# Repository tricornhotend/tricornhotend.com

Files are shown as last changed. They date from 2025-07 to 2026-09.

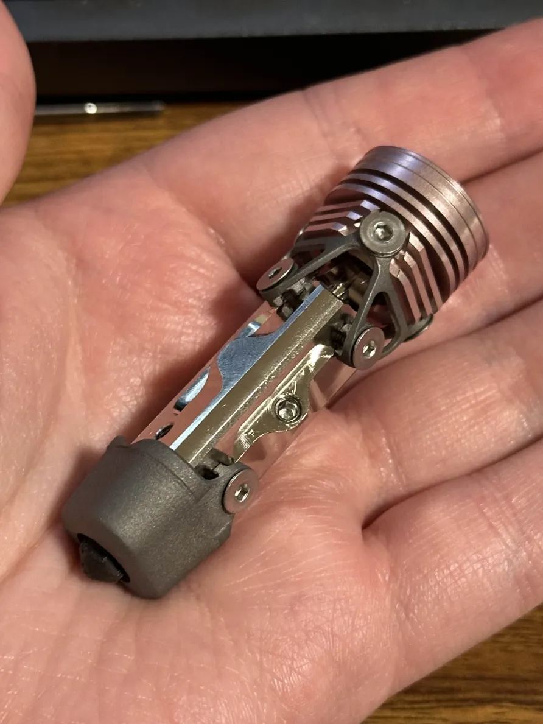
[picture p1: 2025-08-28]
Images/held-tricorn.png

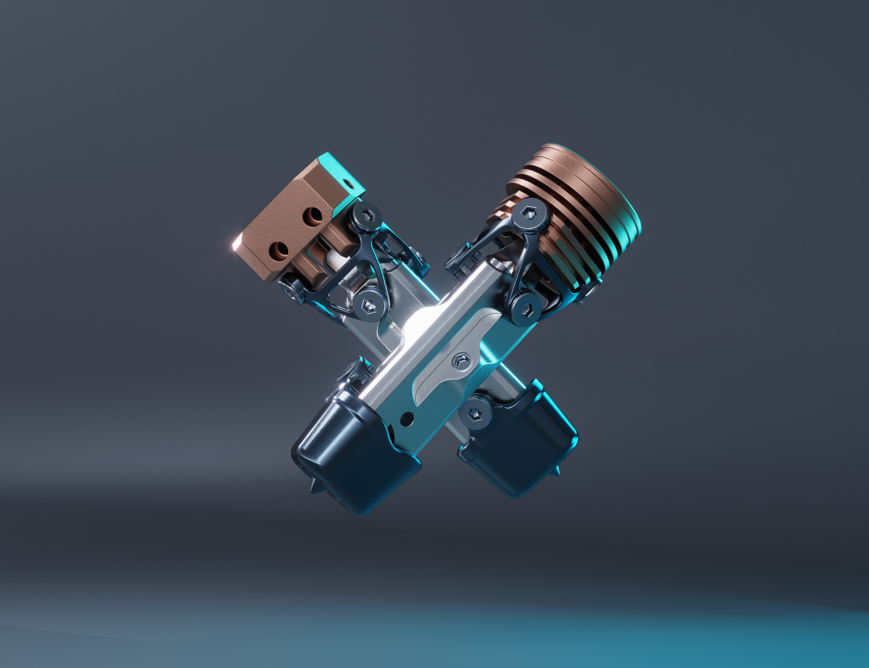
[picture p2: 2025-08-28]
Images/tricornrender.png

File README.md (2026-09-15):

pictures of the hotend cad

Tricorn is a modern open-source hotend featuring mostly standard components while introducing some new ones.
- Inverted heatbreak Tricorn keeps the heatbreak threads out of the meltzone generally improving thermals.
- 4mm Heater cartridges, more combined surface area than 6mm, replacable.
- No screw smaller than m3, everything is either m4 or m3.
- M3 Dragon mounting
- V6 Nozzle Standard
- Air (Fan) or Conduction (Metal plate mounted)
   - (Long) With Hotblock at 260c the Heatsink is passively 118c when unmounted/uncooled in roomtemp env.
- A Long meltzone for it's size.
  - (Long) ~53.5mm with a nozzle, 48mm without.
  - (Short) ~41mm with a nozzle, 35.5mm without.
[Tricorn Website](https://tricornhotend.com)

This project is available under [CC0 1.0 Universal](https://creativecommons.org/publicdomain/zero/1.0/).  
Previous versions were licensed under [CC BY-NC 4.0](https://creativecommons.org/licenses/by-nc/4.0/) and may continue to be used under those terms.  

# Awesome vendors
These are vendors I personally trust to provide a quality version of the hotend, while it can be purchased elsewhere I recommend you purchase from them!

| Vendor | Link | Long | Short |
|---|---|---|---|
| Excit3D | [excit3dprints.com](https://excit3d.shop/shop/tricorn-hotend) | ✅ | ⏲️ |

# Toolhead Support
- [Takeoff toolhead](https://github.com/Kizime123/Takeoff-Toolhead/tree/main) Requires drilling out holes to m3 with a drilling jig.
- [Dual 3628 K3 toolhead](https://github.com/stackingdeezlayers/Annex-K3-SLM-Toolhead)
- ["Trinicorn"](https://github.com/Martin-Ivanc/Trinicorn-Toolhead)

# Hot-end Parts BOM

# Proprietary
- Hot-block
- Heat-sink
- 3x Heaters (D4x40mm, 24v, 40w per, 120w total)
- PT1000 M3x3mm Thermistor
- SLM Shield
- SLM Brace
- Heat-break

# Off The Shelf
- https://www.mcmaster.com/93395A198 (7x structural/shield screws per hot-end)
- https://www.mcmaster.com/92605A522 (3x grub screws per hot-end)
- https://www.mcmaster.com/90666A104 (Optional mounting screws, 4x per hot-end)
- https://www.mcmaster.com/7289A12 (Optional hex key for all screws & heatbreak, 1x)

# General Material recommendations:
- Heatbreak - Ti-6Al-4v (Titanium)
- SLM Shield/Crown - Ti-6Al-4v (Titanium)
- Heatsinks - 6061 Aluminum + (Anodize rose gold)
- Hotblock - UNS C18150 (Copper) + (Electroless Nickel)
- Fasteners - 316 Stainless Steel

# Credit
[Synoon](https://synoon.portfoliobox.net/) - Banner render

# Some other neat hotends
Maybe Tricorn doesn't fit what you are looking for, maybe check out these!  
  
[Chube](https://chubehotend.com/) - Practically indestructible  
[V9](https://www.v9hotend.com/) - Inverted heatbreak & Steel

# Donate
Like the hotend? Doing something cool with the concept? Want to support me?
Protect 🏳️‍⚧️ rights: [https://action.aclu.org/give/now](https://action.aclu.org/give/now)

# Contact
"okuhno" on Discord or whatisupmyhomie@tricornhotend.com

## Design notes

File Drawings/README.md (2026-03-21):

# CAD Drawings
These are not perfect but can be a good starting point for your own drawings.  
However, they should be perfectly viable for producing a Tricorn Hotend in general, though there could be issues.

These are the drawings I used for the production of the prototype hotends and they worked out well in that case.

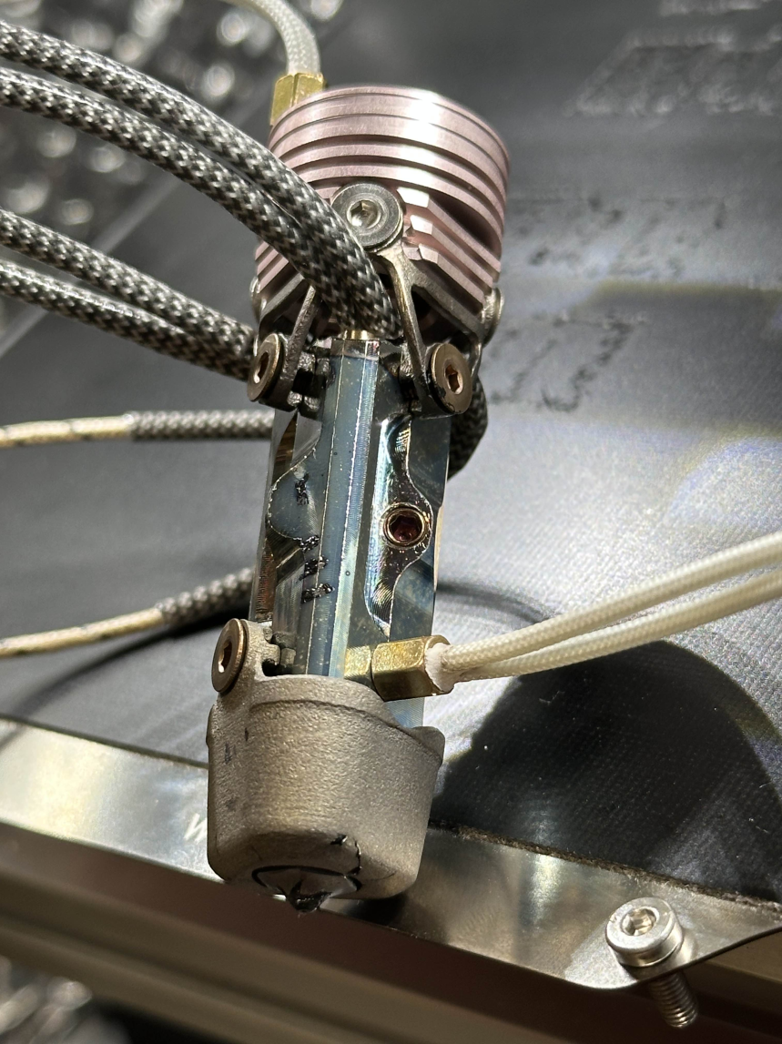
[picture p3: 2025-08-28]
Images/blued-tricorn.png

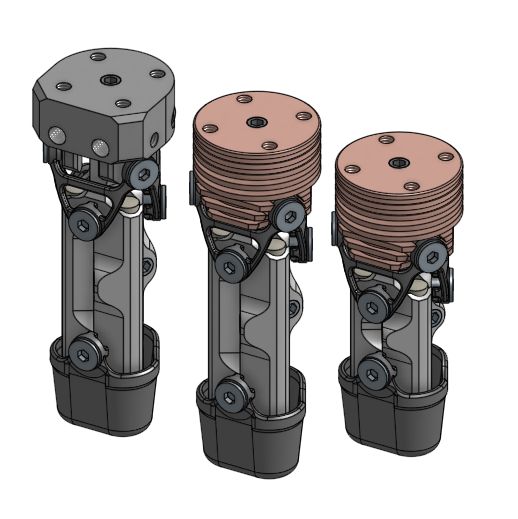
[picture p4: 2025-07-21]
tricorns.png

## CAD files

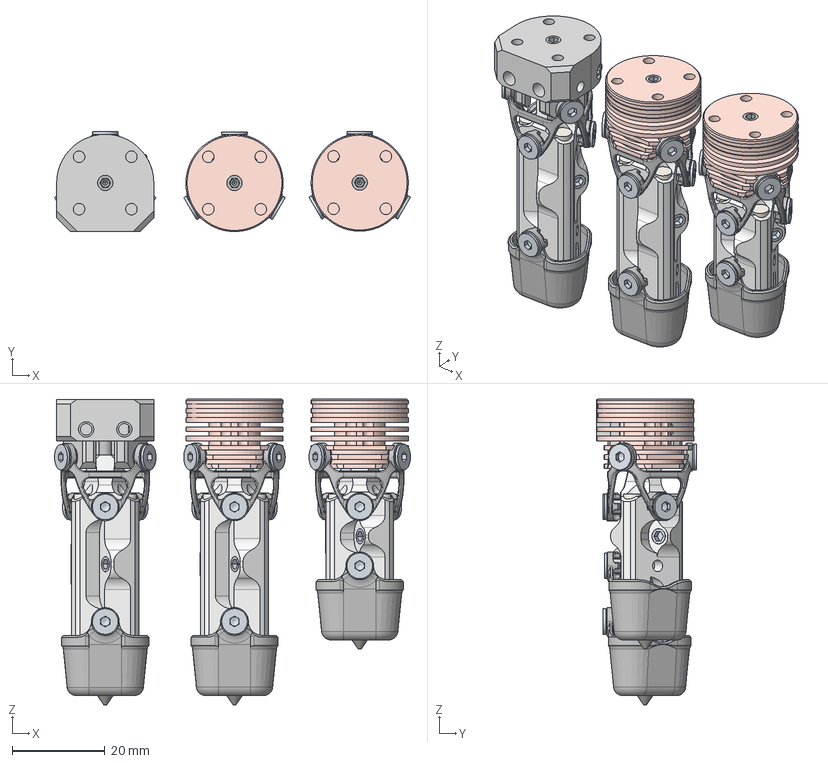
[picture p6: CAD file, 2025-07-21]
Tricorn Hotends.step
76.9 x 21.6 x 66.0 mm
Hex socket countersunk head screw M3x0.5 x 6 x 21
crown x 3
Cup point hex socket set screw M4x0.7 x 4 x 10
nozzle x 3
heatsink x 3
hotblock x 3
heater x 9
heatbreak x 3
bucket x 3

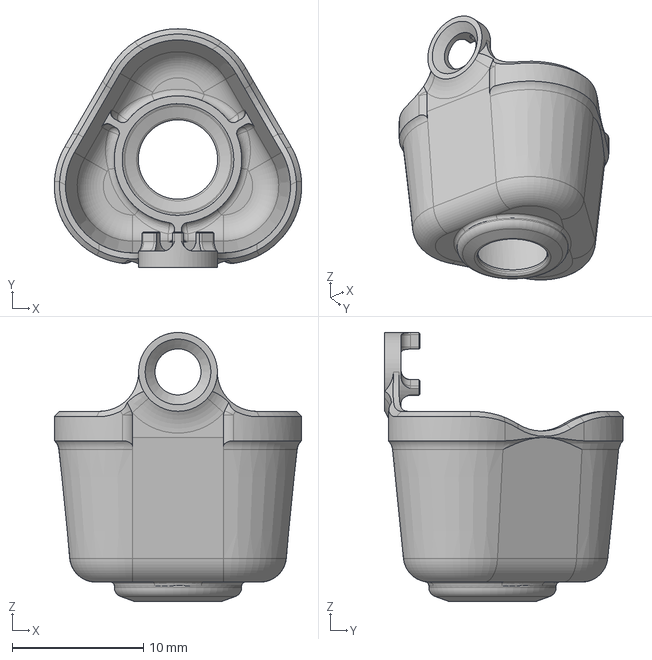
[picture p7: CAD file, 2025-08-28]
Usermods/Burgo Edits/Tricorn v6 covering sheild.step
18.8 x 18.2 x 20.5 mm

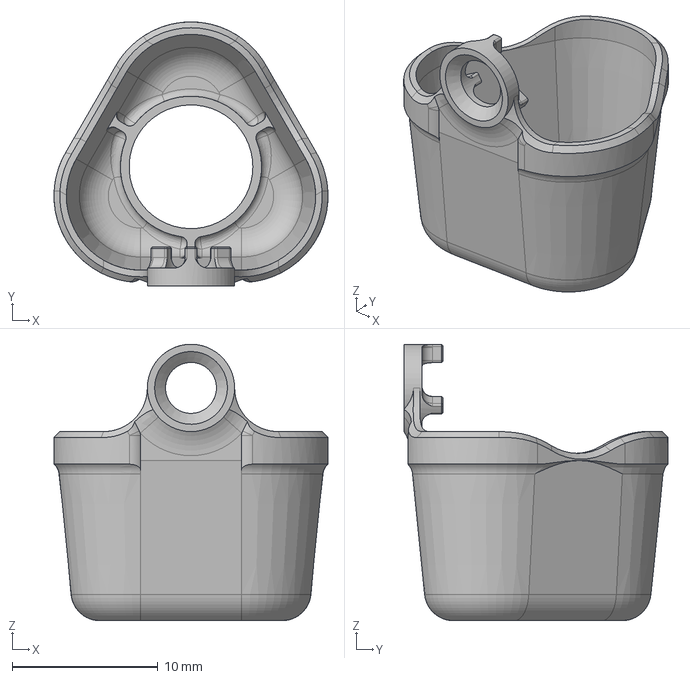
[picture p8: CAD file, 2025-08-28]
Usermods/Burgo Edits/Tricorn 3 prong contact sheild.step
18.8 x 18.2 x 19.0 mm

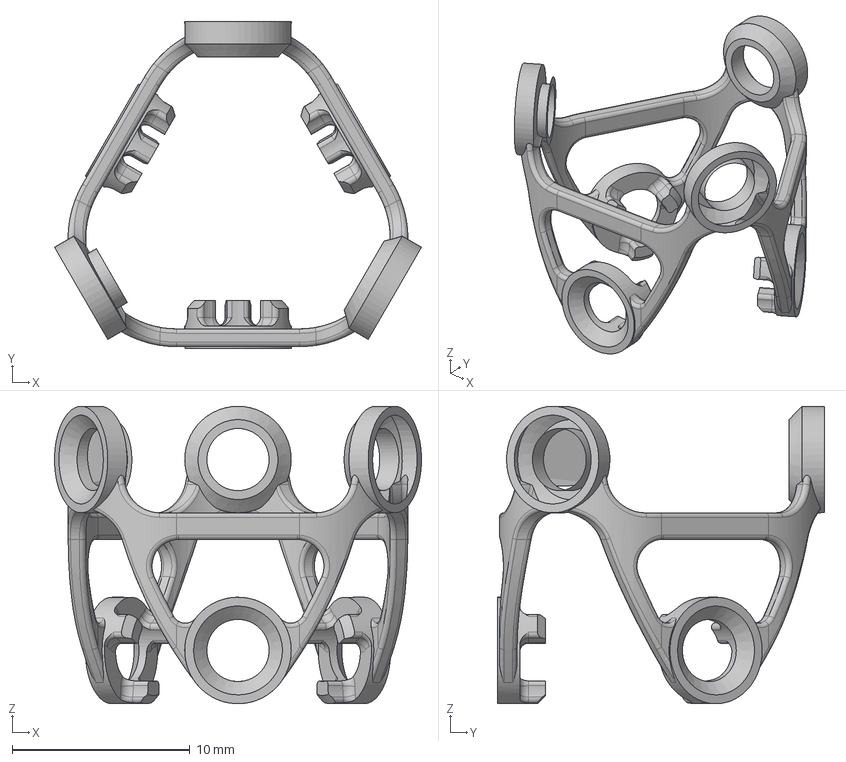
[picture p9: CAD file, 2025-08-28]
Usermods/Burgo Edits/crown 3 point contact.step
20.7 x 18.4 x 16.7 mm

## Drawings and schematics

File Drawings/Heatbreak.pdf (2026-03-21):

A
M4x0.7

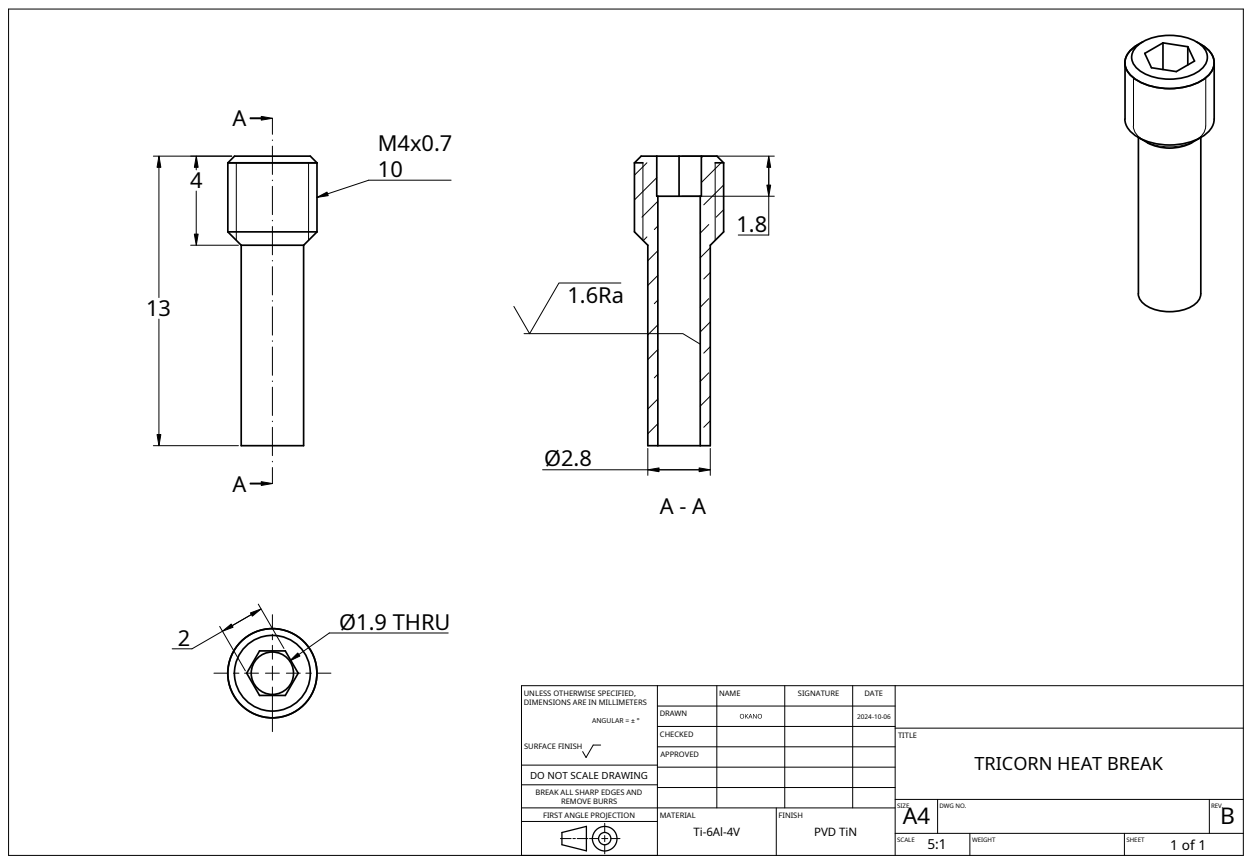
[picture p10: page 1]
MATERIAL Ti-6Al-4V; FINISH; PVD TiN; Ø1.9 THRU

UNLESS OTHERWISE SPECIFIED, DIMENSIONS ARE IN MILLIMETERS ANGULAR = ± ° SURFACE FINISH | | NAME | SIGNATURE | DATE

DRAWN | | | 2024-10-06
CHECKED | | | | TITLE TRICORN HEAT BREAK
APPROVED

DO NOT SCALE DRAWING
BREAK ALL SHARP EDGES AND
REMOVE BURRS
FIRST ANGLE PROJECTION

SIZE A4 | DWG NO. | REV. B

SCALE 5:1 | WEIGHT | SHEET 1 of 1

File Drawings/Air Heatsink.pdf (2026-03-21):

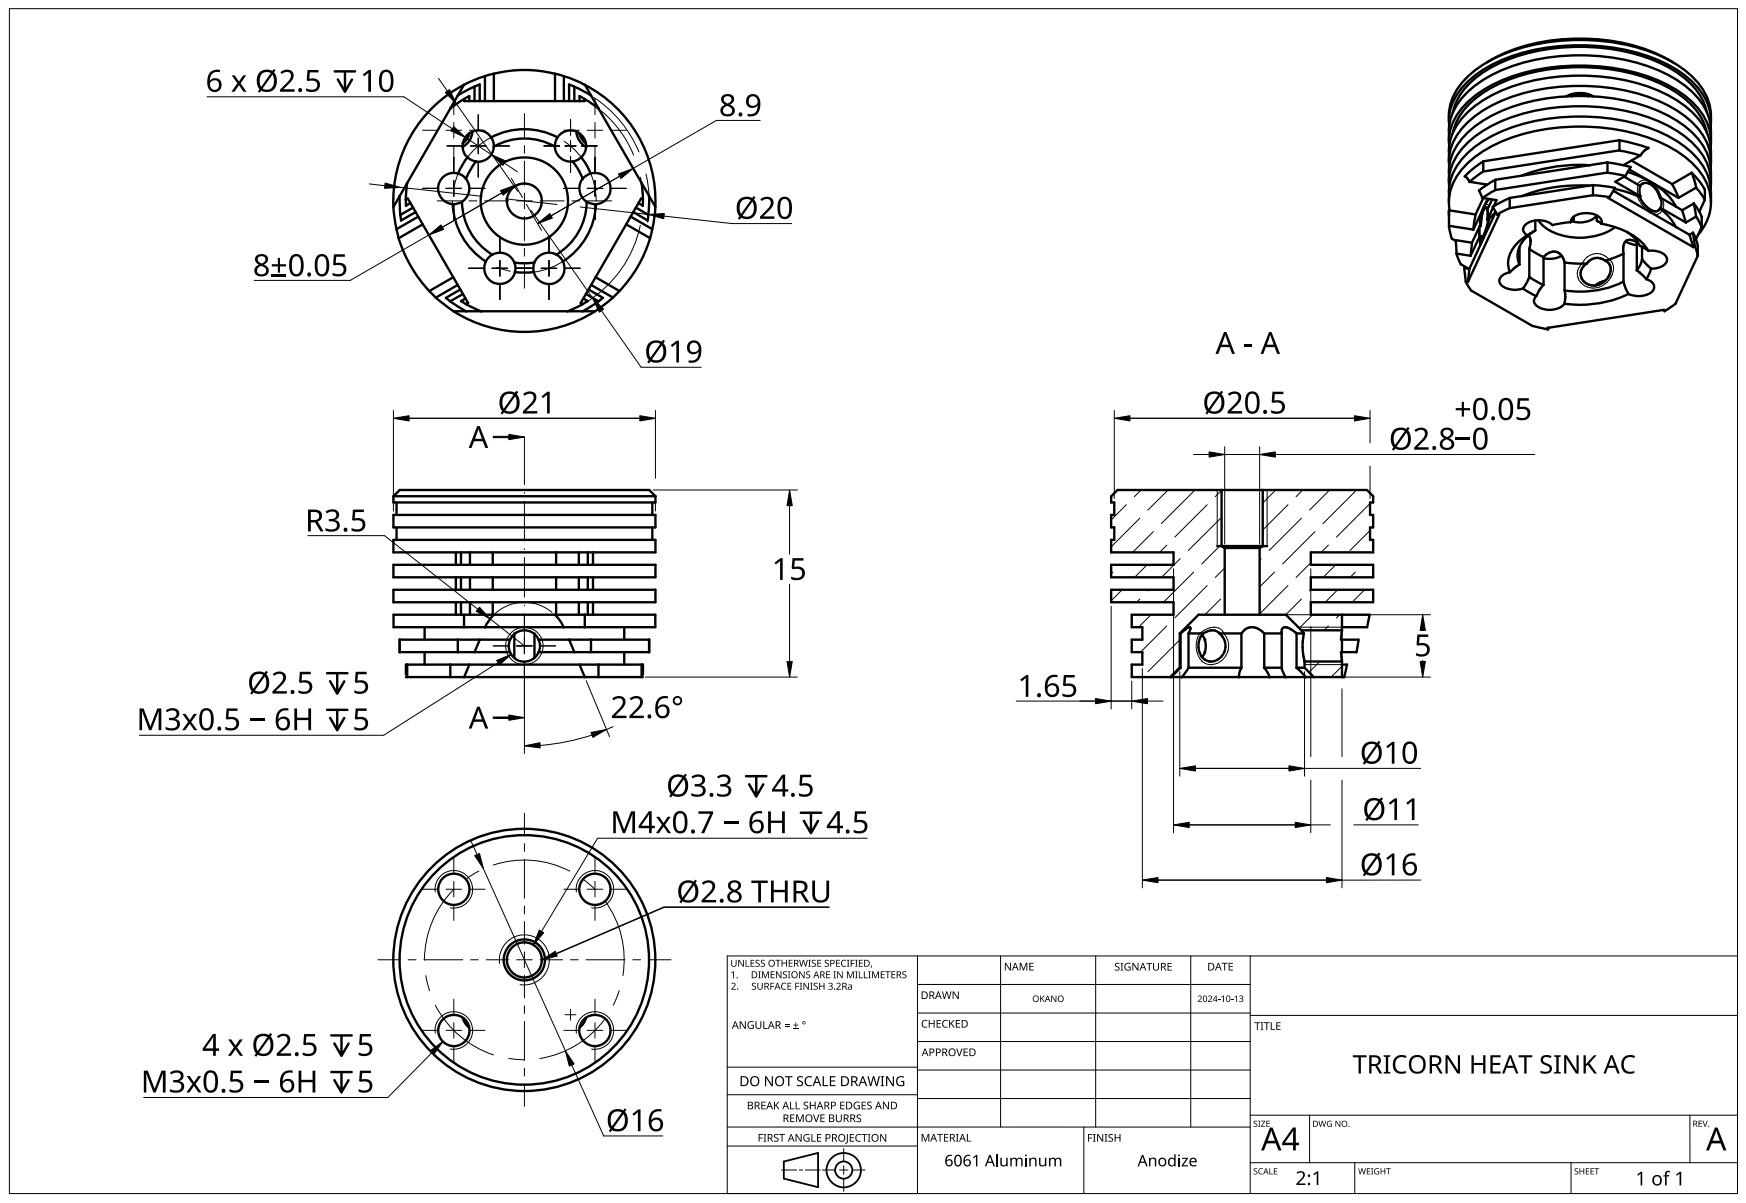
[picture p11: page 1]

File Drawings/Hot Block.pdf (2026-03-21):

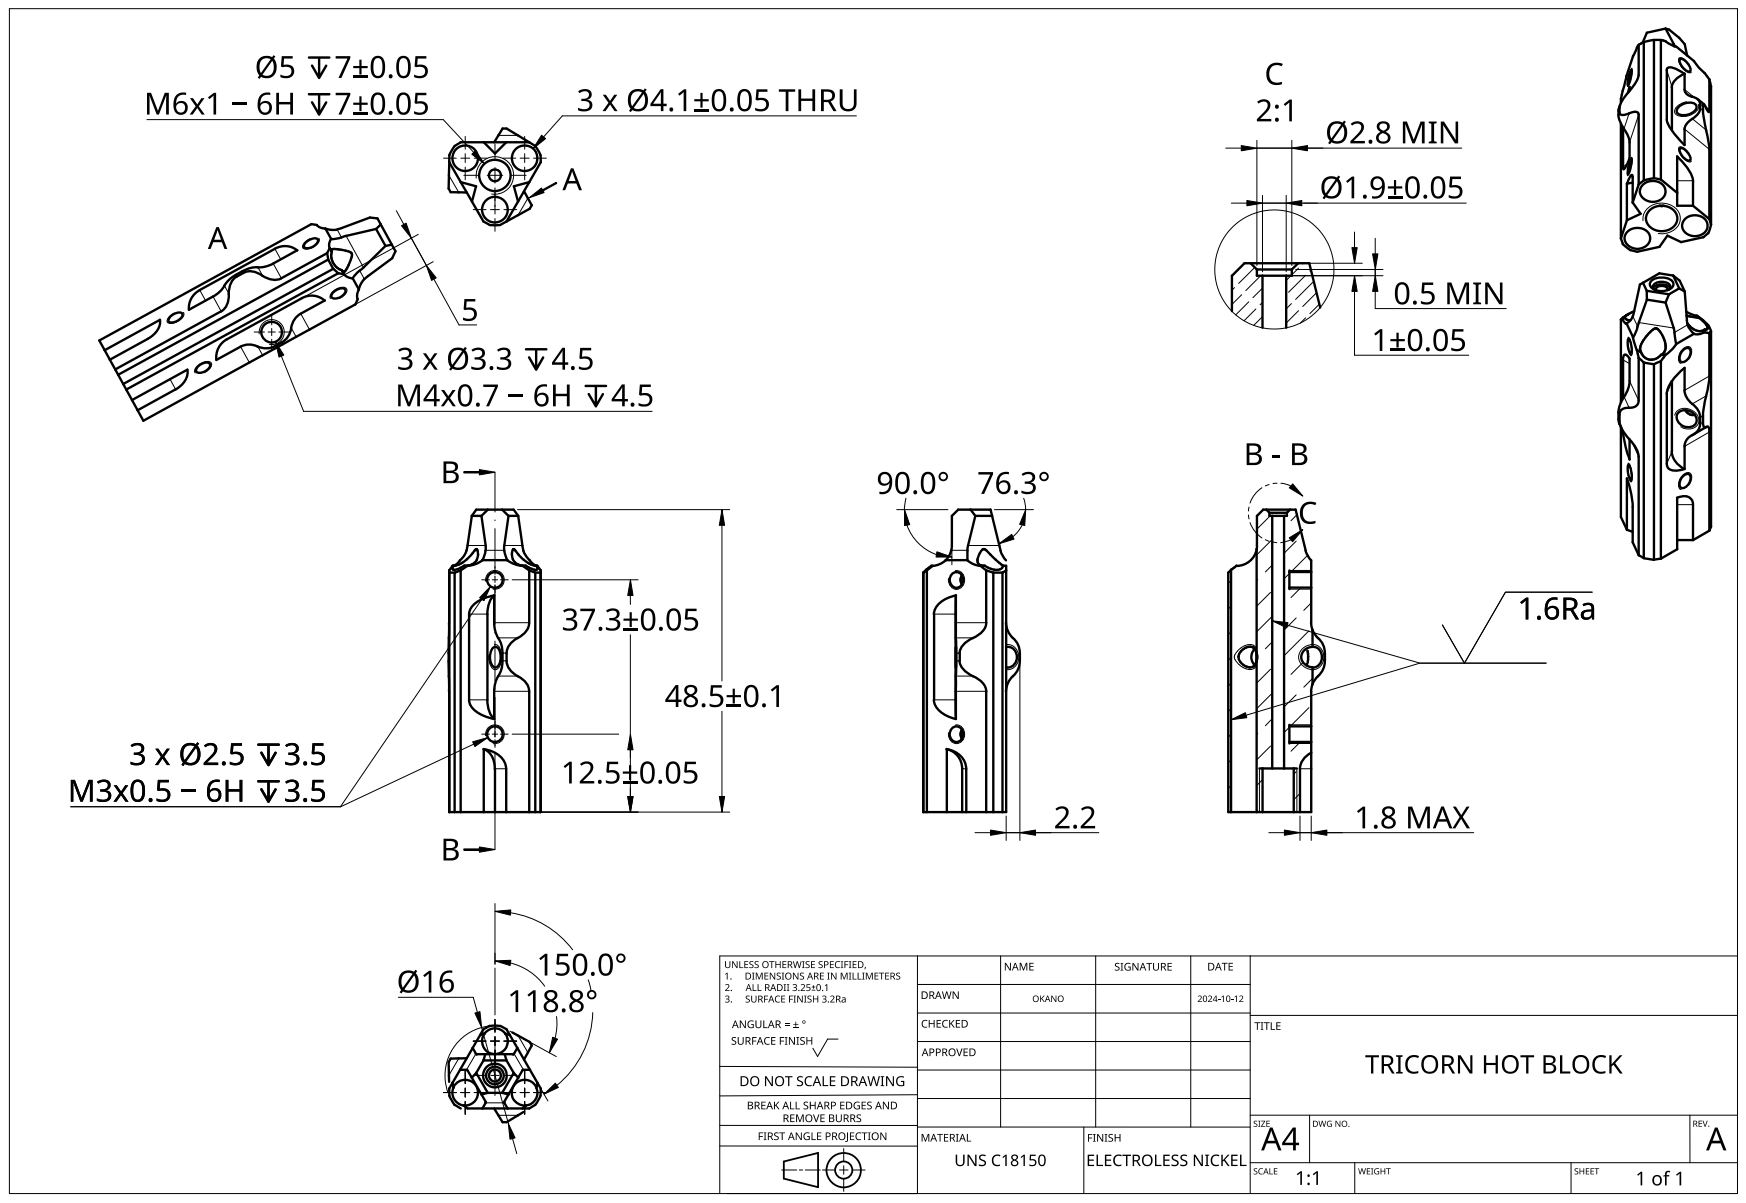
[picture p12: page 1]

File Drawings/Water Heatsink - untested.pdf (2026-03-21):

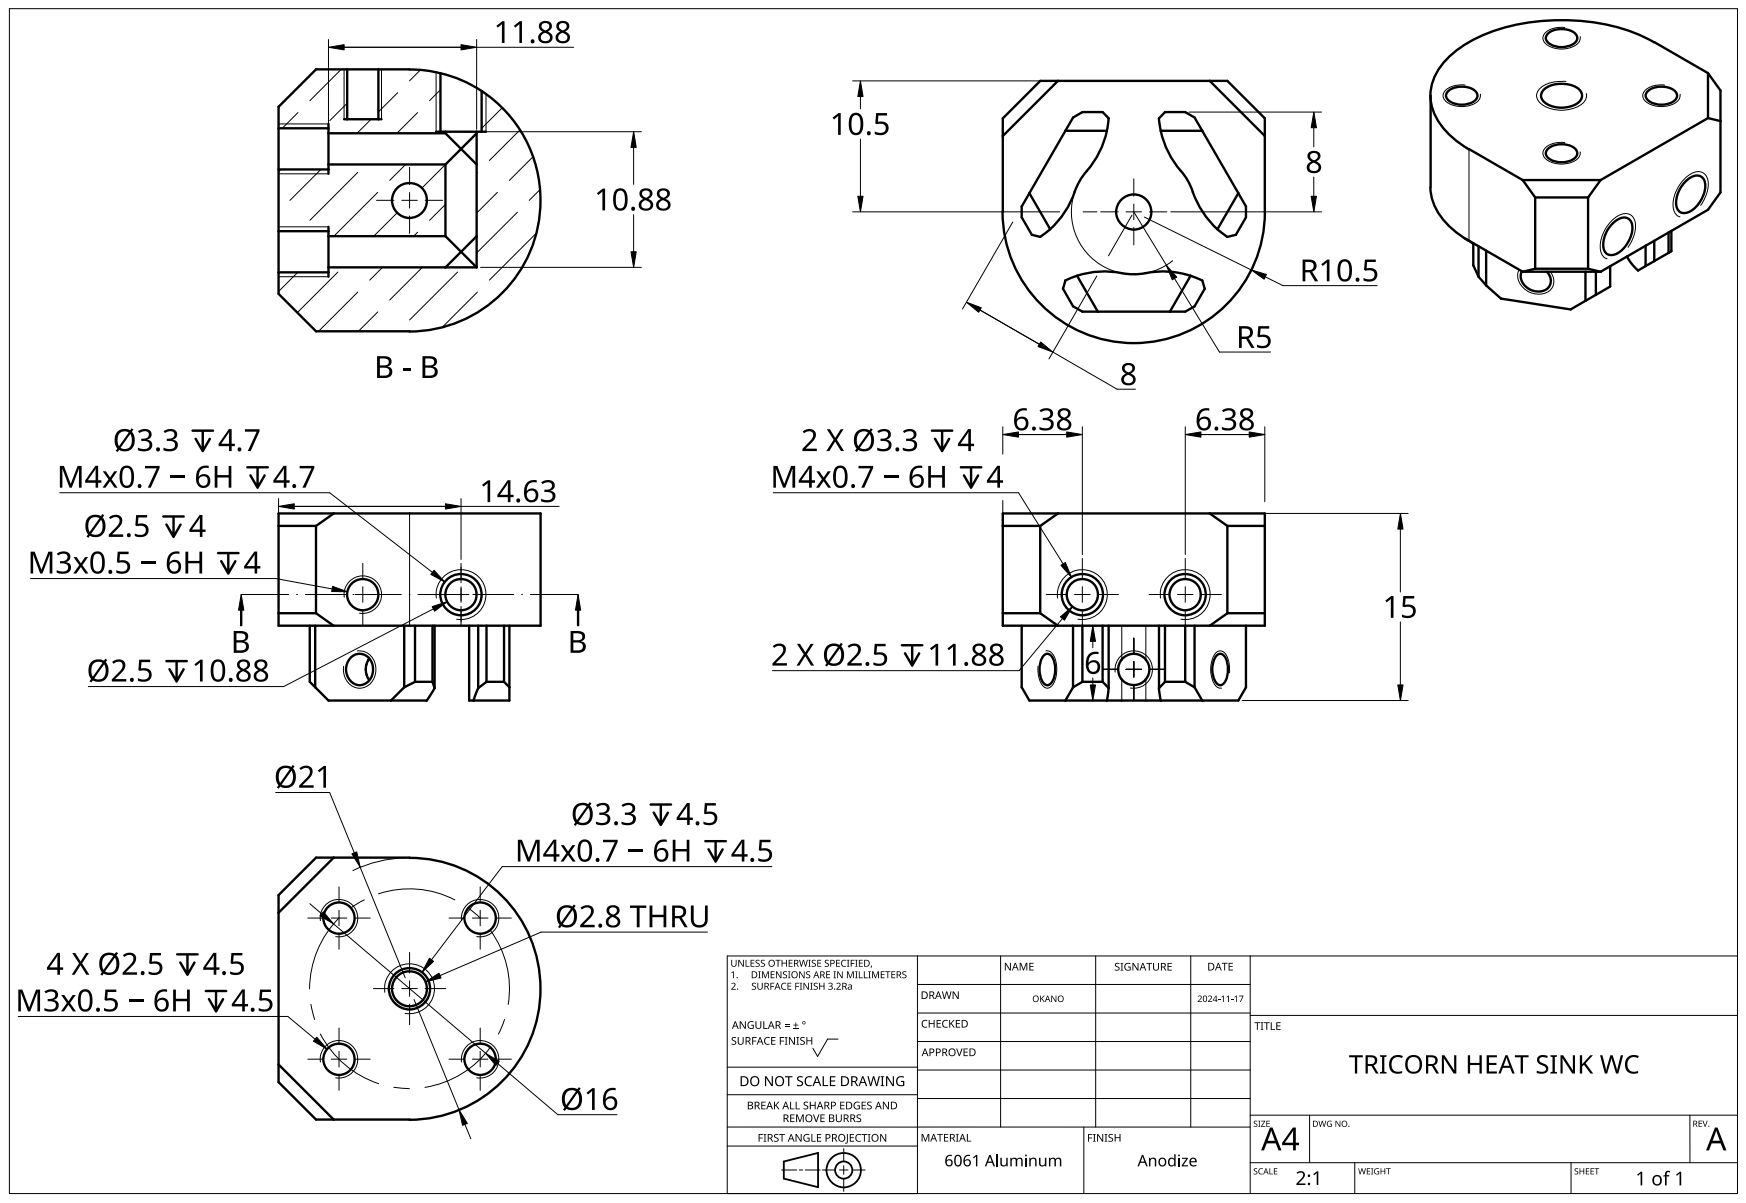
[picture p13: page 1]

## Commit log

2025-07-21 add hotends
    [Tricorn Hotends.step]
2025-08-17 Added Hotend BOM
2025-08-28 add my totally tubular stuff
    [Tricorn 3 prong contact sheild.step, Tricorn v6 covering sheild.step, crown 3 point contact.step]
2025-08-28 add toolhead support section
2025-08-28 Timer update, lettuchead
2026-03-21 Add CAD Drawings
    These can be used to manufacture Tricorn Hot-ends.
2026-03-21 Create README for CAD Drawings
    Added introductory content about CAD drawings and their viability for Tricorn Hotend production.
2026-03-21 Revise vendor trust statement in README
    Updated vendor recommendation for hotend purchase.
2026-03-24 Add Fabreeko as a trusted vendor for hotend
